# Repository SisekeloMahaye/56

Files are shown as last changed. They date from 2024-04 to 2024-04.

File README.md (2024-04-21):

# Group 57 Miro Mouse Project

## Overview
This repository contains the documentation for Group 57's Miro Mouse project. The Miro Mouse is a small robotic platform designed for navigating mazes autonomously.

## Team Members
- MHYSIS001: Responsible for the power subsystem.
- ZKHMUS002: Responsible for the sensing subsystem.

## Subsystems
### Power Subsystem (MHYSIS001)
The power subsystem manages the energy requirements of the Miro Mouse. It includes components such as batteries.

### Sensing Subsystem (ZKHMUS002)
The sensing subsystem is responsible for gathering information about the environment. It includes sensors such as infrared sensors, and any other sensors needed for maze navigation.

## Repository Structure
- `power_subsystem/`: Contains documentation related to the power subsystem.
- `sensing_subsystem/`: Contains documentation related to the sensing subsystem.
- `shared/`: Contains documentation shared between the subsystems.

## Installation
1. Clone this repository to your local machine.
2. Navigate to the relevant subsystem directory (`power_subsystem/` or `sensing_subsystem/`).
3. Follow the instructions in the README file located in each subsystem directory to set up and run the code.

## Contribution Guidelines
If you would like to contribute to this project, please follow these guidelines:
- Fork the repository.
- Create a new branch for your feature or bug fix.
- Make your changes.
- Test your changes thoroughly.
- Create a pull request detailing your changes.

## License
[Creative Commons Attribution 4.0 International license](https://choosealicense.com/licenses/cc-by-4.0/)

## Acknowledgements
- This project is developed as part of [Course EEE3088F] at [University of Cape Town].

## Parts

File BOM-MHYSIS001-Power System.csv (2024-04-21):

Comment | Designator | Footprint | LCSC
100nF | C2,C3,C5,C6 | C_0603_1608Metric | C14663
1nF | C7 | C_0603_1608Metric | C1588
DRV8837 | U1,U3 | WSON-8-1EP_2x2mm_P0.5mm_EP0.9x1.6mm | C191000
10uF | C1,C4 | C_0603_1608Metric | C19702
1k | R1,R2 | R_0603_1608Metric | C21190
RED | D2 | LED_0603_1608Metric | C2286
YELLOW | D1 | LED_0603_1608Metric | C2296
4k | R3 | R_0603_1608Metric | C22978
51k | R4,R5 | R_0603_1608Metric | C23196
SW_SPDT_312 | SW1 | mySwitch | C2890358
TP4056 | U2 | SOIC-8-1EP_3.9x4.9mm_P1.27mm_EP2.29x3mm | C725790

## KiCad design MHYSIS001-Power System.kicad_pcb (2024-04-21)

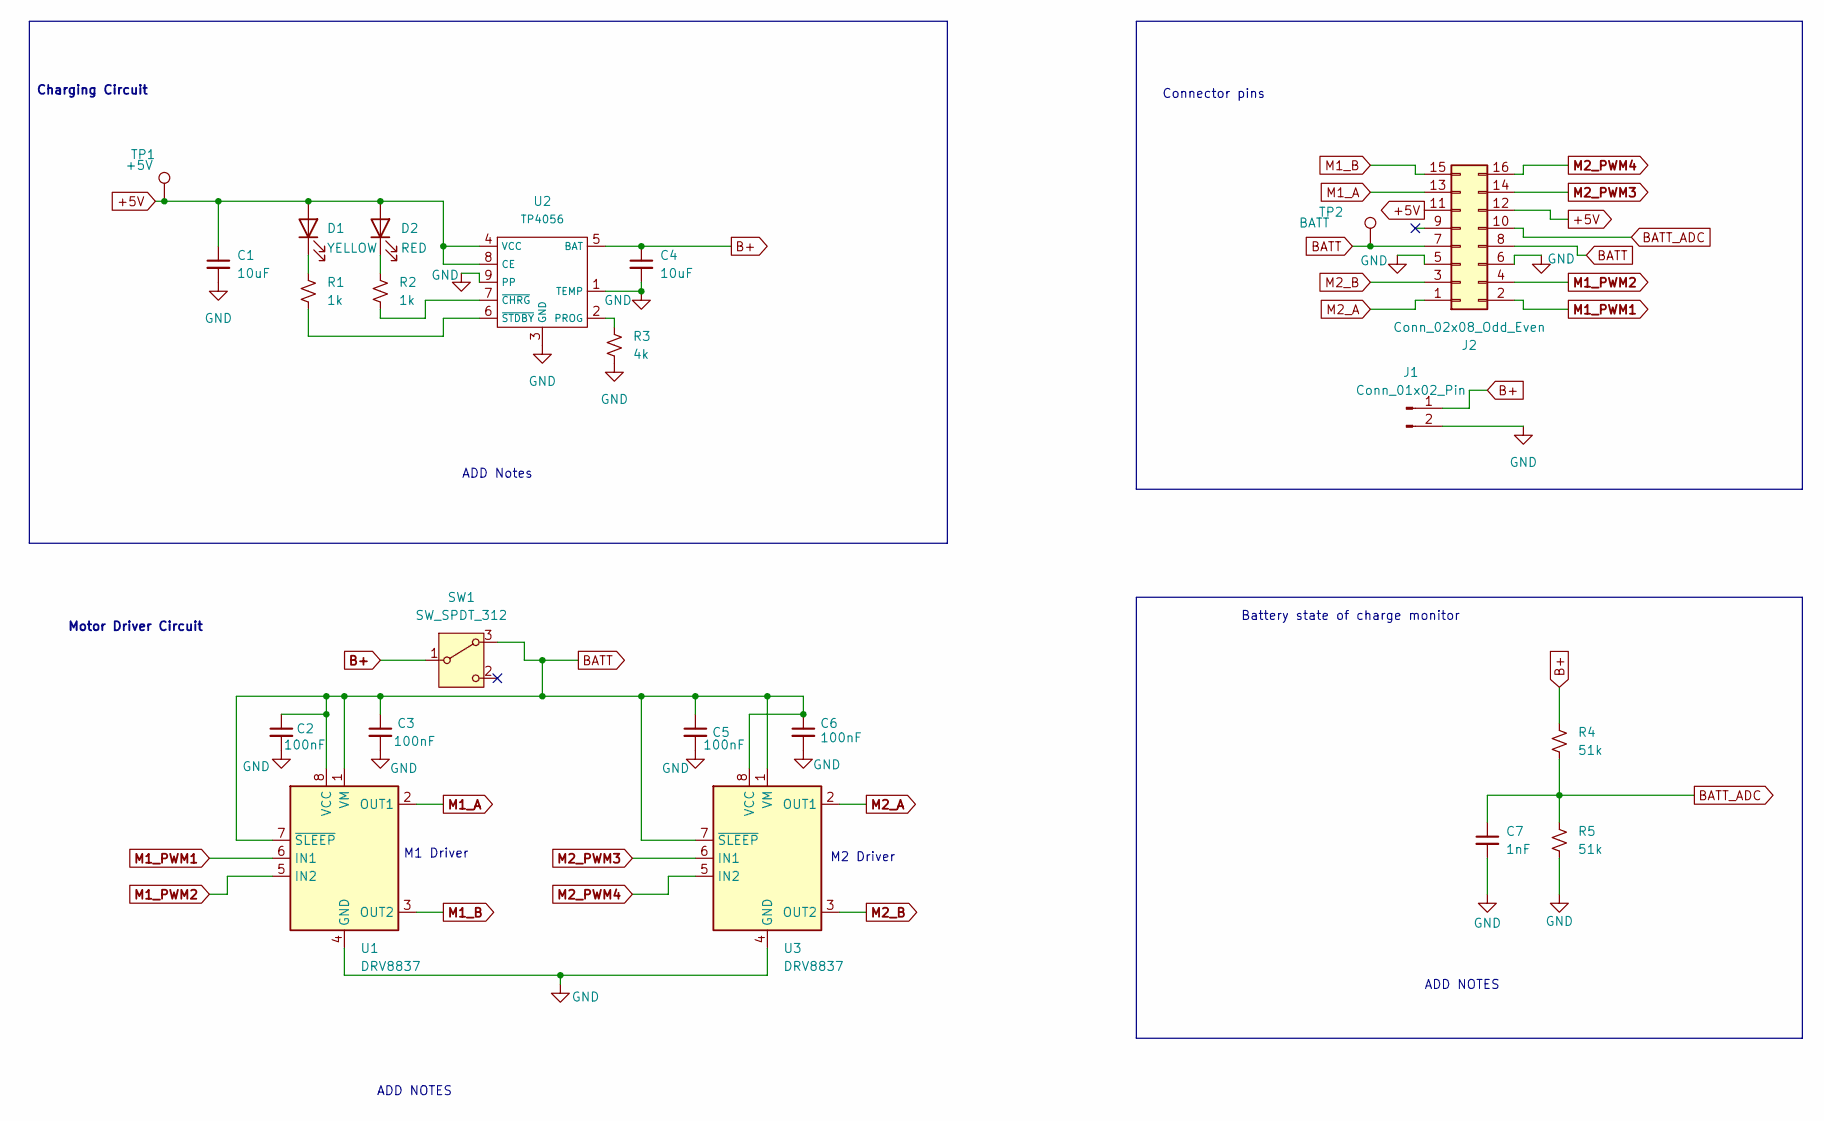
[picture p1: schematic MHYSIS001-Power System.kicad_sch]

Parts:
C1, C4: 10uF; C_0603_1608Metric
C2, C3, C5, C6: 100nF; C_0603_1608Metric
C7: 1nF; C_0603_1608Metric
D1: YELLOW; LED_0603_1608Metric
D2: RED; LED_0603_1608Metric
J1: Conn_01x02_Pin; JST_PH_B2B-PH-K_1x02_P2.00mm_Vertical
J2: Conn_02x08_Odd_Even; PinHeader_2x08_P2.54mm_Vertical
R1, R2: 1k; R_0603_1608Metric
R3: 4k; R_0603_1608Metric
R4, R5: 51k; R_0603_1608Metric
SW1: SW_SPDT_312; mySwitch
TP1: +5V; TestPoint_Pad_D1.0mm
TP2: BATT; TestPoint_Pad_D1.0mm
U1, U3: DRV8837; WSON-8-1EP_2x2mm_P0.5mm_EP0.9x1.6mm
U2: TP4056; SOIC-8-1EP_3.9x4.9mm_P1.27mm_EP2.29x3mm

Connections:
+5V: C1.1, D1.2 (A), D2.2 (A), J2.11, J2.12, TP1.1, U2.4 (VCC), U2.8 (CE)
B+: C4.1, J1.1, R4.1, SW1.1 (B), U2.5 (BAT)
BATT: C2.1, C3.1, C5.1, C6.1, J2.7, J2.8, SW1.3 (A), TP2.1, U1.1 (VM), U1.7 (~SLEEP), U1.8 (VCC), U3.1 (VM), U3.7 (~SLEEP), U3.8 (VCC)
BATT_ADC: C7.1, J2.10, R4.2, R5.1
GND: C1.2, C2.2, C3.2, C4.2, C5.2, C6.2, C7.2, J1.2, J2.5, J2.6, R3.2, R5.2, U1.4 (GND), U1.9 (GND), U2.1 (TEMP), U2.3 (GND), U2.9 (PP), U3.4 (GND), U3.9 (GND)
M1_A: J2.13, U1.2 (OUT1)
M1_B: J2.15, U1.3 (OUT2)
M1_PWM1: J2.2, U1.6 (IN1)
M1_PWM2: J2.4, U1.5 (IN2)
M2_A: J2.1, U3.2 (OUT1)
M2_B: J2.3, U3.3 (OUT2)
M2_PWM3: J2.14, U3.6 (IN1)
M2_PWM4: J2.16, U3.5 (IN2)
unnamed: D1.1 (K), R1.1
unnamed: D2.1 (K), R2.1
unnamed: R3.1, U2.2 (PROG)
unnamed: R2.2, U2.7 (~CHRG)
unnamed: R1.2, U2.6 (~STDBY)

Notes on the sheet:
M2 Driver
M1 Driver
ADD NOTES
Charging Circuit
ADD Notes
Motor Driver Circuit
Battery state of charge monitor
Connector pins

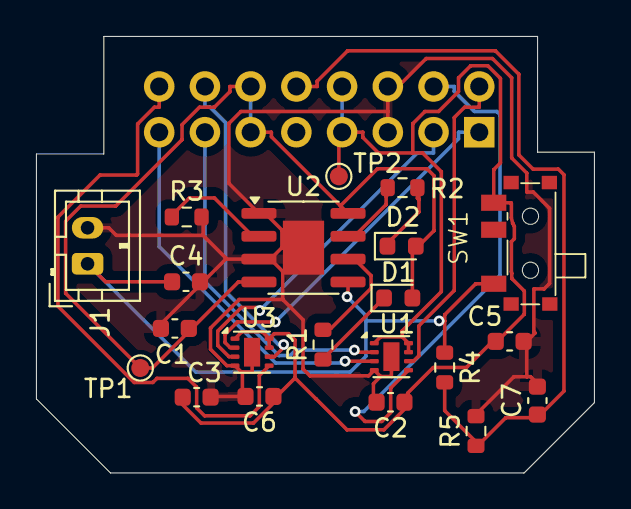
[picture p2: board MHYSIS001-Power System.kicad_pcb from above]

Board: 2 copper layers, 31.0 x 24.2 mm, 22 parts (1 on the bottom side), 18 nets.

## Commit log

2024-04-21 Add files via upload
    Added Gerber files
2024-04-21 Add files via upload
    Added CPL files
    [CPL-MHYSIS001-Power System.csv]
2024-04-21 Add files via upload
    Added BOM file
    [BOM-MHYSIS001-Power System.csv]
2024-04-21 Add files via upload
    Added schematic
    [MHYSIS001-Power System.kicad_sch]
2024-04-21 Add files via upload
    Added PCB file
    [MHYSIS001-Power System.kicad_pcb]
